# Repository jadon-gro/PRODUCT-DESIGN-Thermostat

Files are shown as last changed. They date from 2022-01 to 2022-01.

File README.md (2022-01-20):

# PRODUCT-DESIGN-Thermostat

 

## Introduction
This is a personal project as a self study for product design (CAD, IoT, Arduino etc.).
### Problem
The thermostat in the Georgia Tech apartment I live in is ancient and horrible. It is just a knob labelled "warmer" and "cooler." I wanted to make a device that probes many locations in the apartment and can automatically articulate the knob based on the average temperature.

### Design Goals
I wanted to use a hub that displays:
- The temperature/humidity of the apartment (gateway that can recieve data from many nodes)
- The target temperature (adjustable with buttons)
- The current mode (cooling, warming, or idle)

I also wanted satallite nodes capable of sending temperature/humidity data.

## Hardware
### Hub
1. ESP-32s Microcontroller - https://www.amazon.com/gp/product/B0718T232Z/ref=ppx_yo_dt_b_search_asin_title?ie=UTF8&psc=1
2. Adafruit Monochrome OLED - https://www.adafruit.com/product/326
3. Generic Breadboard Buttons
4. Hatchbox White 1.75mm PLA - https://www.amazon.com/gp/product/B00J0GMMP6/ref=ppx_yo_dt_b_asin_title_o06_s00?ie=UTF8&psc=1
5. Generic Microservo - (I used a really old radioshack one I found in my drawer - I have the same one from many AIBs)

I used an ESP32 as the hub microcontroller for its bluetooth capabilities which I might use later to create a bluetooth app (see future iterations). The faster processor and greater I/O are just bonuses.

### Probe
1. ESP-8266 Microcontroller - https://www.amazon.com/gp/product/B010O1G1ES/ref=ppx_yo_dt_b_search_asin_title?ie=UTF8&th=1
2. SHT31-D Temperature and Humidity Sensor - https://www.amazon.com/gp/product/B085WBFCMF/ref=ppx_yo_dt_b_search_asin_title?ie=UTF8&psc=1
The SHT31-D was chosen because it's got an incredible .3 degree celsius error range, has an integrated heater for getting rid of moisture and is relatively cheap.
Other options from my local microcenter had a many-degree range of error which was unacceptable for my use.

## Design
The 3D model underwent a LARGE number of prototypes and test-prints for fit and ease of use. I settled on a top friction mounted unibody that reaches around to the front where the servo is screwed in place.

The model attaches to the thermostat knob using an independent friction fitted cap that has a slot for the microservo to grab.

Buttons were a difficult part to mount as they are more meant for breadboards. The best solution I found was mounting them on the top leaving holes for the pins to be accessable from the inside.

The model is viewable in the src folder.

## Assembly
### Printing
Cura Slicer Screenshot - Body Cura Slicer Screenshot - Back Cura Slicer Screenshot - Back

Body:
I like to print the whole model in one run using supports and 20% infill (for speed). I printed from back to front which allowed for the best finish on viewable parts, best bed adhesion, and (relatively) easy support removal. Remove the supports from the inside of the body FIRST to reduce risks of breaking the servo arm in the process.

Backplate:
Print the back facing down, with NO supports, and 100% infill. You don't want the clips snapping off and it's a small part so the time save from less infill is minimal.

Knob:
Print with opening facing down using supports. Infill is up to you. This allows for the best finish on the visible portions of the part and a rougher and grippier texture where the part touches the knob.

### Soldering
Assembly from here on is more intuitive and you can probably figure out what works best for your tools and abilities. I will however provide some tips for a few key parts.

PinOut for ESP32 (hub)
| Connection | ESP-32s GPIO Pin |
| --- | --- |
| Servo PWM | 13 |
| Cold Button | 34 |
| Warm Button | 35 |
| Wake Button | 32 |
| OLED MOSI | 23 |
| OLED CLK | 18 |
| OLED DC | 19 |
| OLED CS | 5 |
| OLED Reset | 17 |

Buttons:
First break off one of the pins for two of the buttons. The buttons on either end have an unused pin that conflicts with the mounting holes. Glue the bottom of the buttons to the slots on the main body and have the pins come through to the inside. Now you can solder all the pins (one side high, the other side to corresponding GPIO pin).



Now you can solder appropriate length wire from each component to the microcontroller. I glued the rest of the parts in place with hot glue. Make sure to align the port with the hole and route the servo wires through the smaller hole.

Probe:
Just connect the SHT31 onto the I2C bus of your microcontroller.

I may make an encolsure for this in the future but for now I just have mine on a breadboard on my desk.



## Things That Still Need Doing/Fixing
This took me a little over a week of working on and off so there is plenty still to be done.
1. Proper graphical support for more than one probe
2. Making an enclosure for the probe
3. Making backplate pins that don't interfere with the buttons
4. Making the system adjustable over bluetooth or a web-app (difficult over student wifi)
5. Enabling timeline on Fusion 360 for easier revisions. (I just forgot to)
6. Cable manage the servo (make it look prettier in general)

## Known Issues
- My system randomly reboots sometimes. I think this may have to do with a poor soldering job on my part and pins shorting. I'm working on figuring that out.

If you have any questions about code/design decisions, please feel free to reach out to me via email: jadon.gro@gatech.edu

## Prototype Photos
I did a poor job of keeping track of prototypes but here are the ones I still had by the "end" of the project.

Servo Mount:



Body/Buttons/Backplate:



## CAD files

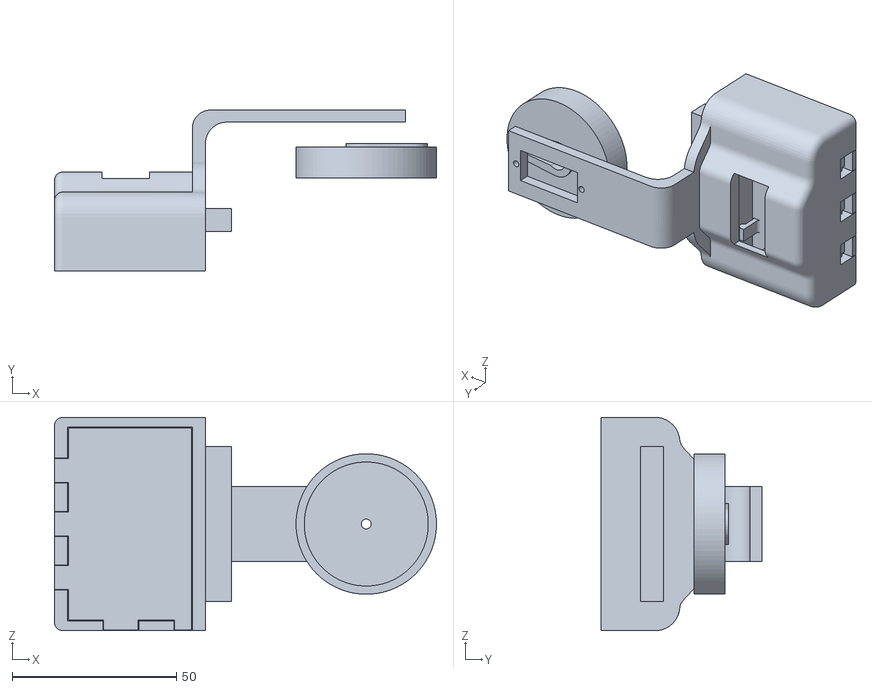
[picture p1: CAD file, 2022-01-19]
src/3D Models/Thermostat Mount v7.stl
116.4 x 49.0 x 65.0

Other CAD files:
src/3D Models/Thermostat Mount v7.f3d

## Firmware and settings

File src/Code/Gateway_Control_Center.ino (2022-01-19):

#include <Arduino.h>
#include <WiFi.h>
#include <esp_now.h>
/**
 * Thermostat control center for ESP-32 board.
 * This is programmed for the SSD1306 OLED screen by adafruit.
 * 
 * Dependencies:
 * ESP32Servo library made by Kevin Harrington
 * Adafruit's GFX and SSD1306 libraries
 * 
 * This program allows the esp32 to manipulate the thermostat with room for error and use buttons
 * to wake the OLED screen and to change the target temperature
 * 
 * The OLED goes to sleep after 2 min of being idle. This is to prevent dimming caused by prolonged
 * on-time
 * 
 * Note: Servo will wiggle around a bit when changing position. This is to solve a problem where
 * my weak old servo would start stalling at the end of a stroke because the knob became too hard to move.
 */

#include <ESP32Servo.h>
#include <SPI.h>
#include <Wire.h>
#include <Adafruit_GFX.h>
#include <Adafruit_SSD1306.h>


// Screen set up -----------------------------------------------------------------------------
#define SCREEN_WIDTH 128 // OLED display width, in pixels
#define SCREEN_HEIGHT 64 // OLED display height, in pixels

// Declaration for SSD1306 display connected using software SPI:
#define OLED_MOSI   23
#define OLED_CLK   18
#define OLED_DC   19
#define OLED_CS    5
#define OLED_RESET 17
Adafruit_SSD1306 display(SCREEN_WIDTH, SCREEN_HEIGHT,
                         OLED_MOSI, OLED_CLK, OLED_DC, OLED_RESET, OLED_CS);
bool displaying = true;
int sleepCounter = 13;





// Servo set up -----------------------------------------------------------------------------
// These are angles. The thermostat has a position for cold, and if the target temperature 
// isn't reached after some time, it moves to colder. Same for hot/hotter
int pos = 65; // initial servo position
int coldPos = 55; 
int colderPos = 5;
int hotPos = 125;
int hotterPos = 175;
float targetTemp = 70.0;
Servo tempservo; // create servo object
int servoPin = 13;


// MISC set up ------------------------------------------------------------------------------
float currTemp[] = {70.0}; // add another entity for every recieving node you have
char *locations[] = {"Jadon's Room"};
int numNodes = 1;
int changeCounter = 0; //counts checks since last change
int checked = 0; // checked is a boolean that prevents the servo from adjusting to default values after a reset
char* message = "idle";



// Button set up --------------------------------------------------------------------------
#define COLD_BUTTON   34
#define WARM_BUTTON   35
#define WAKE_BUTTON   32






/*
 * This is the message struct for recieving data from nodes
 * node ID is user defined and can help make more readable identifiers for nodes
 */
typedef struct message {
  int nodeId;
  float temperature;
  float humidity;
};

struct message myMessage;

void onDataReceiver(const uint8_t * mac, const uint8_t *incomingData, int len) {
  checked = 1;
  Serial.println("Message received.");
  memcpy(&myMessage, incomingData, sizeof(myMessage));
  Serial.println("=== Data ===");
  Serial.print("Mac address: ");
  for (int i = 0; i < 6; i++) {
    Serial.print("0x");
    Serial.print(mac[i], HEX);
    Serial.print(":");
  }
  Serial.print("\n");
  Serial.print(locations[myMessage.nodeId]);
  Serial.print("\n\nTemperature: ");
  Serial.println(myMessage.temperature);
  Serial.print("\n\nHumidity: ");
  Serial.println(myMessage.humidity);
  Serial.println();
  currTemp[myMessage.nodeId] = myMessage.temperature;

}

void setup() {
  Serial.begin(115200);
  // Servo set up -----------------------------------
  // Allow allocation of all timers
  ESP32PWM::allocateTimer(0);
  ESP32PWM::allocateTimer(1);
  ESP32PWM::allocateTimer(2);
  ESP32PWM::allocateTimer(3);
  tempservo.setPeriodHertz(50);    // standard 50 hz servo
  tempservo.attach(servoPin, 685, 3000); // attaches the servo on pin 18 to the servo object
  // different servos may require different min/max settings
  // for an accurate 0 to 180 sweep



  // Wifi set up ------------------------------------
  WiFi.mode(WIFI_STA);

  // Get Mac Add
  Serial.print("Mac Address: ");
  Serial.print(WiFi.macAddress());
  Serial.println("ESP32 ESP-Now Broadcast");

  // Initializing the ESP-NOW
  if (esp_now_init() != 0) {
    Serial.println("Problem during ESP-NOW init");
    return;
  }
  esp_now_register_recv_cb(onDataReceiver);



  // Init screen
  // SSD1306_SWITCHCAPVCC = generate display voltage from 3.3V internally
  if (!display.begin(SSD1306_SWITCHCAPVCC)) {
    Serial.println(F("SSD1306 allocation failed"));
    for (;;); // Don't proceed, loop forever
  }
  display.clearDisplay();
  display.display();

  // Button set up
  pinMode(COLD_BUTTON, INPUT_PULLUP);
  pinMode(WARM_BUTTON, INPUT_PULLUP);
  pinMode(WAKE_BUTTON, INPUT_PULLUP);
  attachInterrupt(digitalPinToInterrupt(COLD_BUTTON), dec, FALLING);
  attachInterrupt(digitalPinToInterrupt(WARM_BUTTON), inc, FALLING);
  attachInterrupt(digitalPinToInterrupt(WAKE_BUTTON), wake, FALLING);


  pos = 90;
  tempservo.write(pos+2);
  delay(500);
  tempservo.write(pos-2);
  delay(500);
  tempservo.write(pos);
}

void loop() {
  float avgTemp = average(currTemp, numNodes);
  Serial.print("\n\n== Average temp check ==\n Average Temp:");
  Serial.println(avgTemp);
  Serial.println("========================\n\n");


  /*
   * This whole structure is the meat of the program and controls the servo
   * 
   * If the average temperature is more than .7 degree from the target temperature,
   * the servo will move to correct for this. Either it will move to "hotpos" or "coldpos"
   * If the target temperature hasn't been reached for 15 min, it will move to a more severe position,
   * i.e. "hotterpos" or "colderpos". If the target temperature has been reached withing 1.4 degrees,
   * the servo will move back to idle.
   */
  if (checked) {
    if (targetTemp - avgTemp > .7) {
      Serial.println("Making warmer");
      if (changeCounter == 0 && (pos == hotPos || pos == hotterPos)) {
        message = "warming+";
        pos = hotterPos;
        tempservo.write(pos + 3);
        delay(500);
        tempservo.write(pos);
      } else if (changeCounter < 30) {
        message = "warming";
        pos = hotPos;
        tempservo.write(pos + 3);
        delay(500);
        tempservo.write(pos);
      }

      changeCounter = 90; // waits 90*10 seconds (15 min) before changing again
    } else if (targetTemp - avgTemp < -.7) {
      Serial.println("Making colder");
      if (changeCounter == 0 && (pos == coldPos || pos == colderPos)) {
        message = "cooling+";
        pos = colderPos;
        tempservo.write(pos - 3);
        delay(500);
        tempservo.write(pos);
      } else if (changeCounter < 30) {
        message = "cooling";
        pos = coldPos;
        tempservo.write(pos - 3);
        delay(500);
        tempservo.write(pos);
      }

      changeCounter = 90; // waits 90*10 seconds (15 min) before changing again
    } else { // settles down to a normal temp
      message = "idle";
      if (pos > 90) {
        pos = 115;
        delay(500);
        tempservo.write(pos);
      }
      if (pos < 90) {
        pos = 65;
        tempservo.write(pos - 3);
        delay(500);
        tempservo.write(pos);
      }

    }
    if (changeCounter != 0) {
      changeCounter--;
    }
  }
  // Display routine
  updateDisplay();

  delay(10000); // 10 seconds delay between checks
}
/*
 * This method updates the display
 * 
 * This is governed by the displaying boolean which will become false after 2 min of no activity
 */
void updateDisplay(void) {
  if (displaying) {
    display.clearDisplay();
    display.setTextSize(2); // Draw 2X-scale text
    display.setTextColor(SSD1306_WHITE);
    display.setCursor(0, 0);
    display.print(targetTemp, 1);
    display.cp437(true);
    display.setCursor(70, 5);
    display.setTextSize(1);
    display.print(message);
    display.drawLine(51, 0, 51, 17, SSD1306_WHITE);
    display.drawLine(0, 17, 51, 17, SSD1306_WHITE);
    display.setTextSize(1);
    for (int i = 0; i < numNodes; i++) {
      display.setCursor(0, (3 + (i * 3)) * 8);
      if (i == 0) {
        display.print("Jadon's Room:");
      }

      display.setCursor(0, (4 + (i * 3)) * 8);
      display.print("    Temp:     ");
      display.print(myMessage.temperature);
      display.write(248);
      display.println("F");
      display.print("    Humidity: ");
      display.print(myMessage.humidity);
      display.print("%");
    }
    if (sleepCounter == 0) {
      displaying = false;
      display.clearDisplay();
      display.setCursor(80, 28);
      display.print("sleeping...");
      display.display();
      delay(2000);
      display.clearDisplay();
      display.display();
    } else {
      sleepCounter--;
    }
    display.display();





  }
}

// This method just takes the average of an array
float average (float * array, int len)  // assuming array is int.
{
  float sum = 0.0;  // sum will be larger than an item, long for safety.
  for (int i = 0; i < len; i++)
    sum += array [i];
  return  ((float) sum) / (float)len;
}

// ISR for cooling button. This also debounces.
void dec()
{
  static unsigned long last_interrupt_time = 0;
  unsigned long interrupt_time = millis();
  // If interrupts come faster than 200ms, assume it's a bounce and ignore
  if (interrupt_time - last_interrupt_time > 200)
  {

    sleepCounter = 12;
    displaying = true; // wake
    targetTemp = targetTemp - .1; // decrement target temp by .1 degrees
    updateDisplay(); // update display
  }
  last_interrupt_time = interrupt_time;
}

// ISR for warming button. This also debounces.
void inc()
{
  static unsigned long last_interrupt_time = 0;
  unsigned long interrupt_time = millis();
  // If interrupts come faster than 200ms, assume it's a bounce and ignore
  if (interrupt_time - last_interrupt_time > 200)
  {

    sleepCounter = 12;
    displaying = true; // wake
    targetTemp = targetTemp + .1; // increment target temp by .1 degrees
    updateDisplay(); // update display
  }
  last_interrupt_time = interrupt_time;
}

// ISR for wake button. This also debounces.
void wake()
{
  static unsigned long last_interrupt_time = 0;
  unsigned long interrupt_time = millis();
  // If interrupts come faster than 200ms, assume it's a bounce and ignore
  if (interrupt_time - last_interrupt_time > 200)
  {
    sleepCounter = 12;
    displaying = true; // wake

    updateDisplay();
  }
  last_interrupt_time = interrupt_time;
}

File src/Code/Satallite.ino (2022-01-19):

/**
* Satallite probe for sending temperature and humidity data to the thermostat.
* This is coded for an ESP8266 using a SHT31-D temperature module
* 
* This program uses the ESP-NOW protocol developed for the ESP boards by espressif
* 
* Make sure to install the Adafruit SHT31 library which seems to work fine for the
* module I linked in the GitHub README on amazon for cheaper
*
* Version: 1.1
* Author: Jadon G
*/
 
#include <Arduino.h>
#include <ESP8266WiFi.h>
#include <espnow.h>
#include <Wire.h>
#include "Adafruit_SHT31.h"
uint8_t loopCnt = 0;

// ID of the node 
#define id 0;

Adafruit_SHT31 sht31 = Adafruit_SHT31();

// MAC ADDRESS of the 
uint8_t peer1[] = {0x40, 0x91, 0x51, 0xAB, 0x63, 0xF8};

 /**
  * This is the structure for the message
  * 
  * The node ID is a user defined integer that relays the 
  * identity of the probe to the hub in a more readable way than
  * the MAC address. This also allows you to make custom names like "jadon's room"
  * on the receiving end for display purposes.
  * 
  * The temperature and humidity properities are what they're named
  */
typedef struct message {
  int nodeId;
  float temperature;
  float humidity;
};
 
struct message myMessage;


 // Serial monitor sent status for debugging
void onSent(uint8_t *mac_addr, uint8_t sendStatus) {
 Serial.println("Status:");
 Serial.println(sendStatus);
}
 
void setup() {
 Serial.begin(115200);
 
 
 WiFi.mode(WIFI_STA);
 
 // Get Mac Add
 Serial.print("Mac Address: ");
 Serial.print(WiFi.macAddress());
 Serial.println("ESP-Now Sender");
 
 // Initializing the ESP-NOW
 if (esp_now_init() != 0) {
   Serial.println("Problem during ESP-NOW init");
   return;
 }
 
 esp_now_set_self_role(ESP_NOW_ROLE_CONTROLLER);
 // Register the peer
 Serial.println("Registering a peer");
 esp_now_add_peer(peer1, ESP_NOW_ROLE_SLAVE, 1, NULL, 0);
 Serial.println("Registering send callback function");
 esp_now_register_send_cb(onSent);



 //temp sensor init
  if (! sht31.begin(0x44)) {   // Set to 0x45 for alternate i2c addr
    Serial.println("Couldn't find SHT31");
    while (1) delay(1);
  }

  Serial.print("Heater Enabled State: ");
  if (sht31.isHeaterEnabled())
    Serial.println("ENABLED");
  else
    Serial.println("DISABLED");
}
 
void loop() {

  //read the data from the sensor
 float temperatureC = sht31.readTemperature();
 float humidity = sht31.readHumidity();

 //send the data
  if (! isnan(temperatureC)) {  // check if 'is not a number'
    Serial.print("Temp *C = "); Serial.print(temperatureC); Serial.print("\t\t");
    float temperatureF = (temperatureC * 9.0 / 5.0) + 32.0; // convert to fahrenheit
    Serial.print("Temp *F = "); Serial.print(temperatureF); Serial.print("\t\t");
    myMessage.temperature = temperatureF;
  } else { 
    Serial.println("Failed to read temperature");
  }
  if (! isnan(humidity)) {  // check if 'is not a number'
    Serial.print("Hum. % = "); Serial.println(humidity);
    myMessage.humidity = humidity;
  } else { 
    Serial.println("Failed to read humidity");
  }
 
 myMessage.nodeId = id; // assign the ID to the message


 // Send the message
 Serial.println("Send a new message");
 esp_now_send(NULL, (uint8_t *) &myMessage, sizeof(myMessage));

 
 delay(10000);
  /*
   * This a heating cycle that occurs once every 5 minuites and takes 1 min
   * This is necessary so that moisture doesn't accumulate on the sensor
   * No measurements will be taken during the cycle to prevent innacurate data (due to heating)
   * 
   * The first 30 seconds is heating and the second 30 seconds is for cooling down
   */
 if (++loopCnt == 30) {
    sht31.heater(true);
    Serial.println("Heating Sensor...");
    for (int i = 1; i < 31; i++) {
      delay(1000);
      Serial.print("Heater on for ");
      Serial.print(i);
      Serial.println("/30 seconds");
    }
    sht31.heater(false);
    for (int i = 1; i < 31; i++) {
      delay(1000);
      Serial.print("Sensor cooling for ");
      Serial.print(i);
      Serial.println("/30 seconds");
    }

    loopCnt = 0;
  }
 
}

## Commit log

2022-01-19 Code and Model
    [Thermostat Mount v7.f3d]
2022-01-19 added stl for viewing
    [Thermostat Mount v7.stl]
